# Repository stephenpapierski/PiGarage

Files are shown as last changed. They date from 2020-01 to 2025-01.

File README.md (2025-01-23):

> [!IMPORTANT]
> This never worked well and there are much better solutions out there. I would recommend taking a look at [Konnected](https://konnected.io/collections/shop-now?filter.p.tag=Smart+Garage+Door+Openers) Garage Door Openers, which support Hubitat, Home Assistant, Control4 and other cloud based home automation platforms.
# PiGarage
This project contains the Raspberry Pi and Hubitat driver code for a Raspberry Pi hat for controlling a garage door through Hubitat. The hardware includes a relay for actuating the garage door controller, 2 door sensor inputs (open/closed), and status LEDs to communicate door status.

See the [project wiki](https://github.com/stephenpapierski/PiGarage/wiki) to get started.

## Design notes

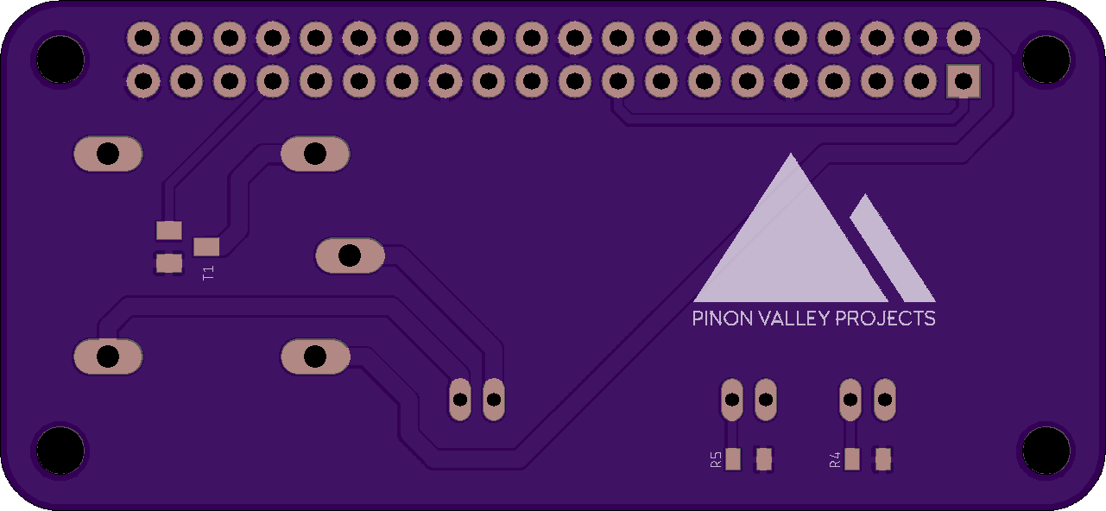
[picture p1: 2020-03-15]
pcb/PiGarage_RENDER_BOTTOM.png

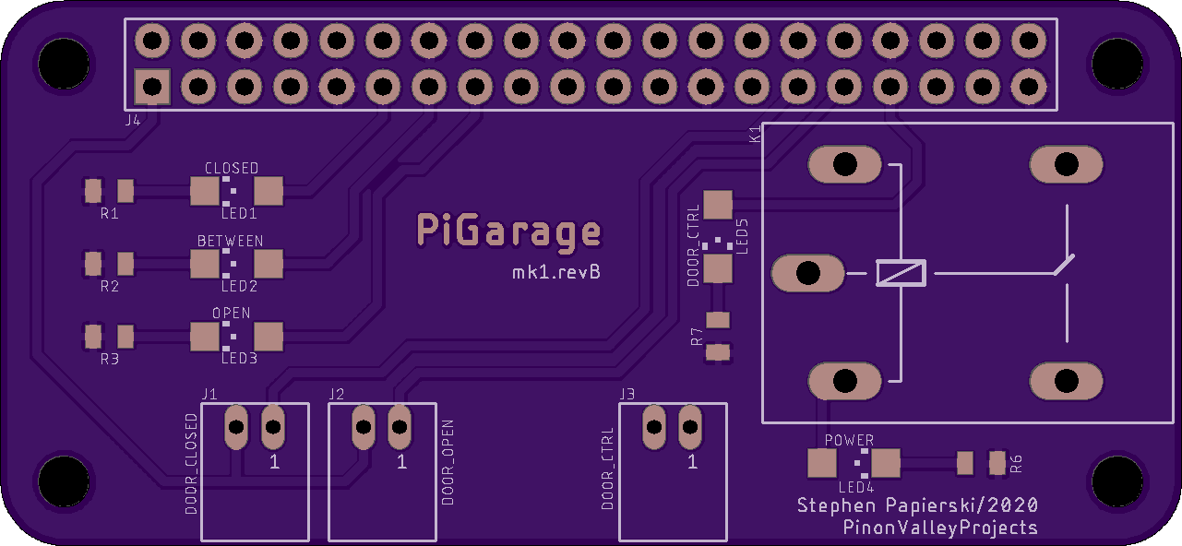
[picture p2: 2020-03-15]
pcb/PiGarage_RENDER_TOP.png

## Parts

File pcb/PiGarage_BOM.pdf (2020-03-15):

Description | Manufacturer | Part # | Device | Package Value Reference Designator Vendor Unit Cost Quantity Extended Cost Shipping Total | Link
2x20 Header | Pololu | 1037 RPI-GPIO-20x2 | J4 | Pololu | $1.25 | 1 | $1.25 | $1.25 https://www.pololu.com/product/1037
M2.5 Standoffs (4-pack) | Pololu | 1952 | | | | | Pololu | $1.39 | 1 | $1.39 | $1.39 https://www.pololu.com/product/1952
M2.5 Screws (25-pack) | Pololu | 1968 | | | | | Pololu | $0.99 | 1 | $0.99 | $0.99 https://www.pololu.com/product/1968
M2.5 Nuts (25-pack) | Pololu | 1967 | | | | | Pololu | $0.99 | 1 | $0.99 | $0.99 https://www.pololu.com/product/1967
$4.95 | $9.57
Relay | Omron | G5LE-1A4 DC5 | G5LE | | | K1 | Digi-Key | $1.41 | 1 | $1.41 | $1.41 https://www.digikey.com/product-detail/en/omron-electronics-inc-emc-div/G5LE-1A4-DC5/Z3116-ND/369019
Relay Driver | ON Semiconductor | NUD3105LT1G | NUD3105 | SOT23 | | T1 | Digi-Key | $0.44 | 1 | $0.44 | $0.44 https://www.digikey.com/product-detail/en/on-semiconductor/NUD3105LT1G/NUD3105LT1GOSCT-ND/1139972
120 Ohm LED Resistor | Yageo | AC0805FR-07120RL RESISTOR_0805 | 0805 | 120 | R2 | Digi-Key | $0.10 | 1 | $0.10 | $0.10 https://www.digikey.com/product-detail/en/yageo/AC0805FR-07120RL/YAG5353CT-ND/7063696
150 Ohm LED Resistor | Yageo | AC0805FR-07150RL RESISTOR_0805 | 0805 | 150 | R3 | Digi-Key | $0.10 | 1 | $0.10 | $0.10 https://www.digikey.com/product-detail/en/yageo/AC0805FR-07150RL/YAG3694CT-ND/6006543
200 Ohm LED Resistor | Yageo | AC0805FR-07200RL RESISTOR_0805 | 0805 | 200 | R1 | Digi-Key | $0.10 | 1 | $0.10 | $0.10 https://www.digikey.com/product-detail/en/yageo/AC0805FR-07200RL/YAG3707CT-ND/6006556
680 Ohm LED Resistor | Yageo | AC0805JR-07680RL RESISTOR_0805 | 0805 | 680 | R6 | Digi-Key | $0.10 | 1 | $0.10 | $0.10 https://www.digikey.com/product-detail/en/yageo/AC0805JR-07680RL/YAG3800CT-ND/6006649
10k Resistor | Yageo | AC0805FR-0710KL | RESISTOR_0805 | 0805 | 10k | R4, R5 | Digi-Key | $0.10 | 1 | $0.10 | $0.10 https://www.digikey.com/product-detail/en/yageo/AC0805FR-0710KL/311-10KLGCT-ND/2828155
Door Ctrl LED Resistor | DNP R7 | $0.00
Green Closed LED | Broadcom Limited | HSMG-C150 | CHIPLED_1206 | 1206 | | LED1 | Digi-Key | $0.50 | 1 | $0.50 | $0.50 https://www.digikey.com/product-detail/en/broadcom-limited/HSMG-C150/516-1443-1-ND/637767
Yellow In Between LED | Broadcom Limited | HSMY-C150 | CHIPLED_1206 | 1206 | | LED2 | Digi-Key | $0.53 | 1 | $0.53 | $0.53 https://www.digikey.com/product-detail/en/broadcom-limited/HSMY-C150/516-1442-1-ND/637766
Red Open LED | Broadcom Limited | HSMS-C150 | CHIPLED_1206 | 1206 | | LED3 | Digi-Key | $0.53 | 1 | $0.53 | $0.53 https://www.digikey.com/product-detail/en/broadcom-limited/HSMS-C150/516-1440-1-ND/637764
Blue PWR LED | Broadcom Limited | HSMN-C150 | CHIPLED_1206 | 1206 | | LED4 | Digi-Key | $1.05 | 1 | $1.05 | $1.05 https://www.digikey.com/product-detail/en/broadcom-limited/HSMN-C150/516-1446-1-ND/637770
Door Ctrl LED | DNP LED5 | $0.00
Door Sensor | SparkFun Electronics COM-13247 | Digi-Key | $3.50 | 2 | $7.00 | $7.00 https://www.digikey.com/product-detail/en/sparkfun-electronics/COM-13247/1568-1607-ND/7229877
JST Connector and Wire Assembly SparkFun Electronics PRT-09914 | JST_2PIN_HEADER | J1, J2, J3 | Digi-Key | $0.95 | 3 | $2.85 | $2.85 https://www.digikey.com/product-detail/en/sparkfun-electronics/PRT-09914/1568-1568-ND/6833927
| | | | | | | | | | | $8.99 $23.80
Circuit Board | Osh Park | PiGarage mk1.revA | $16.35 | 1 | $15.10 | $15.10 https://oshpark.com/shared_projects/nDRBJeuH
| | | | | | $0.00 $15.10
Total | $48.47

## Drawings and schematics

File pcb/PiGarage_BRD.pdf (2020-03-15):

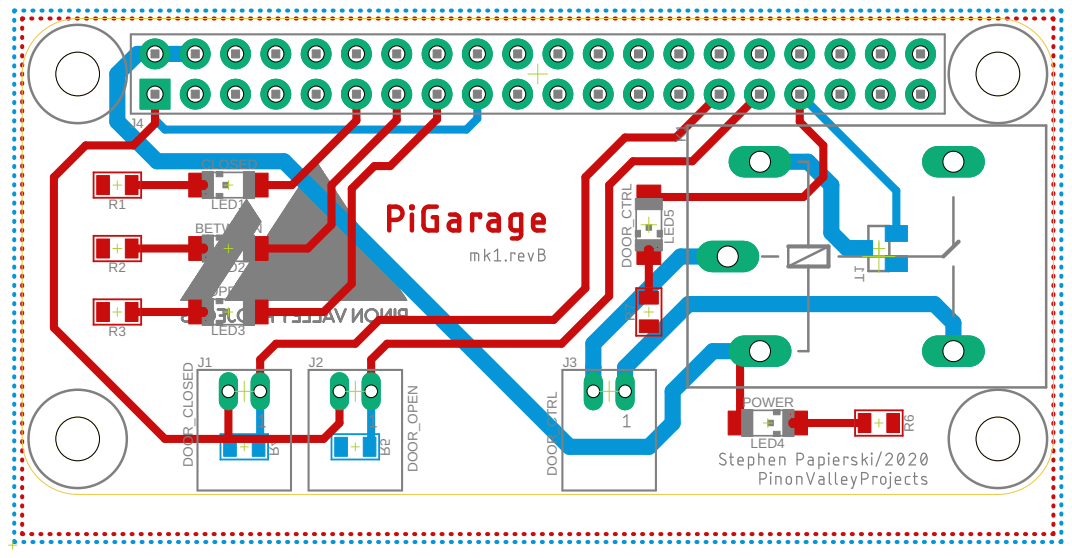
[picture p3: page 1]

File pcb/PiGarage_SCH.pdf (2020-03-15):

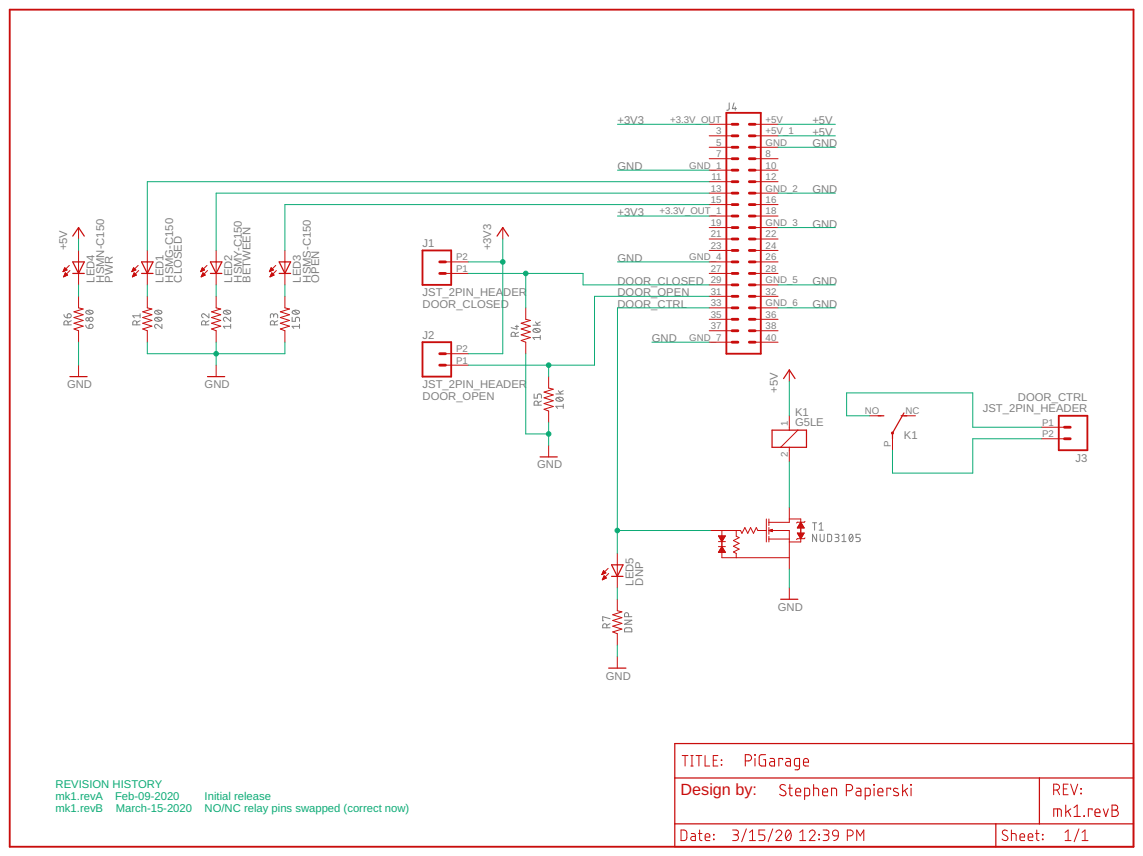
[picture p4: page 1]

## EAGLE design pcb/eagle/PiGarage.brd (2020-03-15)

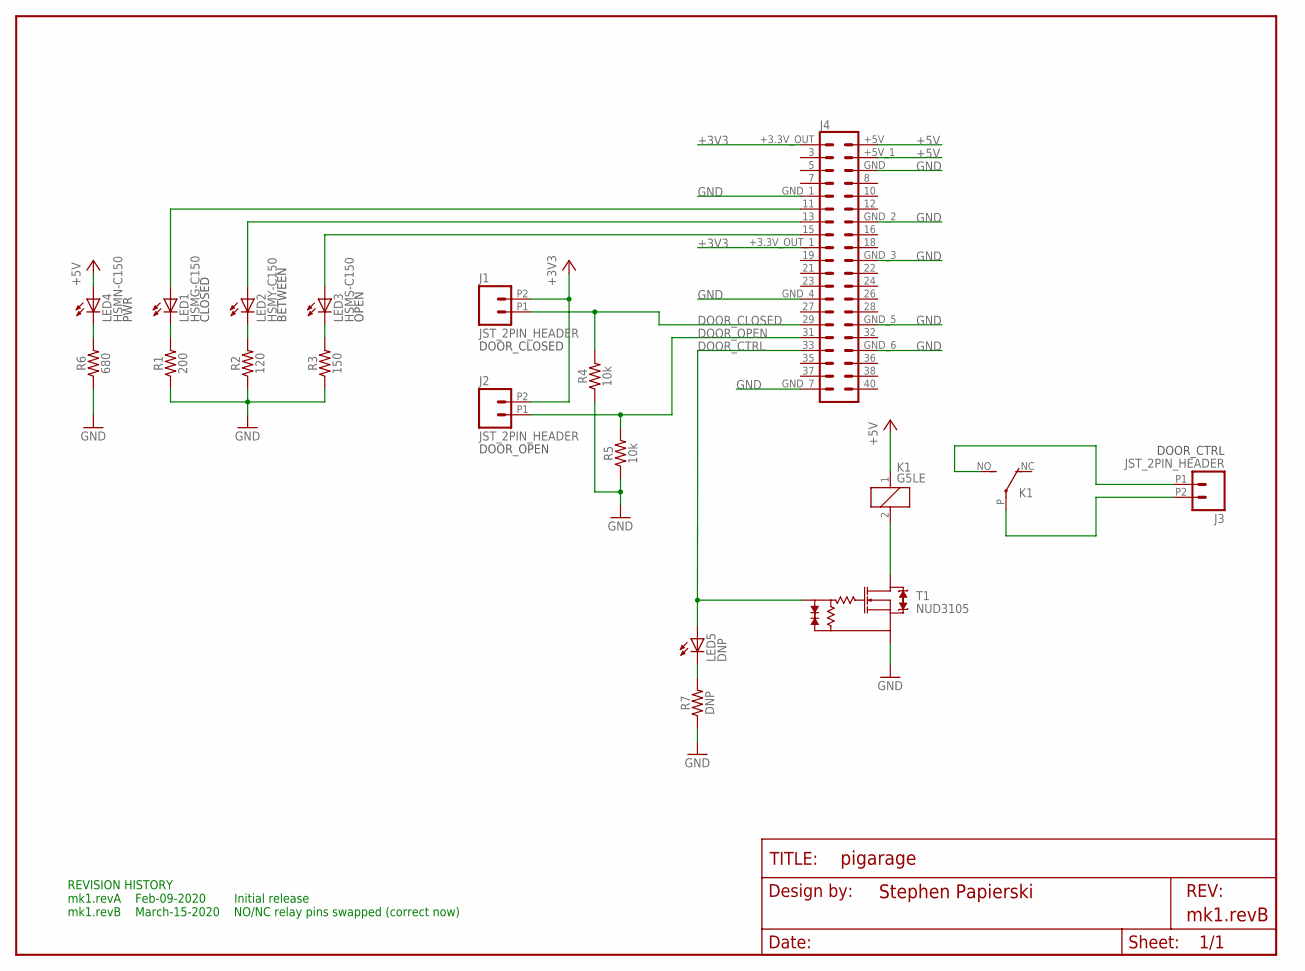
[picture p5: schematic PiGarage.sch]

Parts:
FRAME1: FRAME-LETTERNO_PACKAGE; DUMMY
J1, J2, J3: JST_2PIN_HEADER; JST_2PIN_RIGHT_HEADER
J4: RPI-GPIO-20X2
K1: G5LE
LED1: HSMG-C150; CHIPLED_1206
LED2: HSMY-C150; CHIPLED_1206
LED3: HSMS-C150; CHIPLED_1206
LED4: HSMN-C150; CHIPLED_1206
LED5: DNP; CHIPLED_1206
R1: 200; 0805
R2: 120; 0805
R3: 150; 0805
R4, R5: 10k; 0805
R6: 680; 0805
R7: DNP; 0805
T1: NUD3105; SOT23

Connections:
+3V3: J1.P2 (2), J2.P2 (2), J4.+3.3V_OUT (1), J4.+3.3V_OUT_1 (17)
+5V: J4.+5V (2), J4.+5V_1 (4), K1.1, LED4.A
DOOR_CLOSED: J1.P1 (1), J4.29, R4.2
DOOR_CTRL: J4.33, LED5.A, T1.1 (G)
DOOR_OPEN: J2.P1 (1), J4.31, R5.2
GND: J4.GND (6), J4.GND_1 (9), J4.GND_2 (14), J4.GND_3 (20), J4.GND_4 (25), J4.GND_5 (30), J4.GND_6 (34), J4.GND_7 (39), R1.1, R2.1, R3.1, R4.1, R5.1, R6.1, R7.1, T1.2 (S)
unnamed: K1.2, T1.3 (D)
unnamed: LED5.C, R7.2
unnamed: J3.P1 (1), K1.NO
unnamed: J3.P2 (2), K1.P
unnamed: LED4.C, R6.2
unnamed: J4.11, LED1.A
unnamed: J4.13, LED2.A
unnamed: J4.15, LED3.A
unnamed: LED1.C, R1.2
unnamed: LED2.C, R2.2
unnamed: LED3.C, R3.2

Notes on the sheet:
CLOSED
BETWEEN
OPEN
PWR
DOOR_CLOSED
DOOR_OPEN
DOOR_CTRL
REVISION HISTORY mk1.revA Feb-09-2020 Initial release mk1.revB March-15-2020 NO/NC relay pins swapped (correct now)

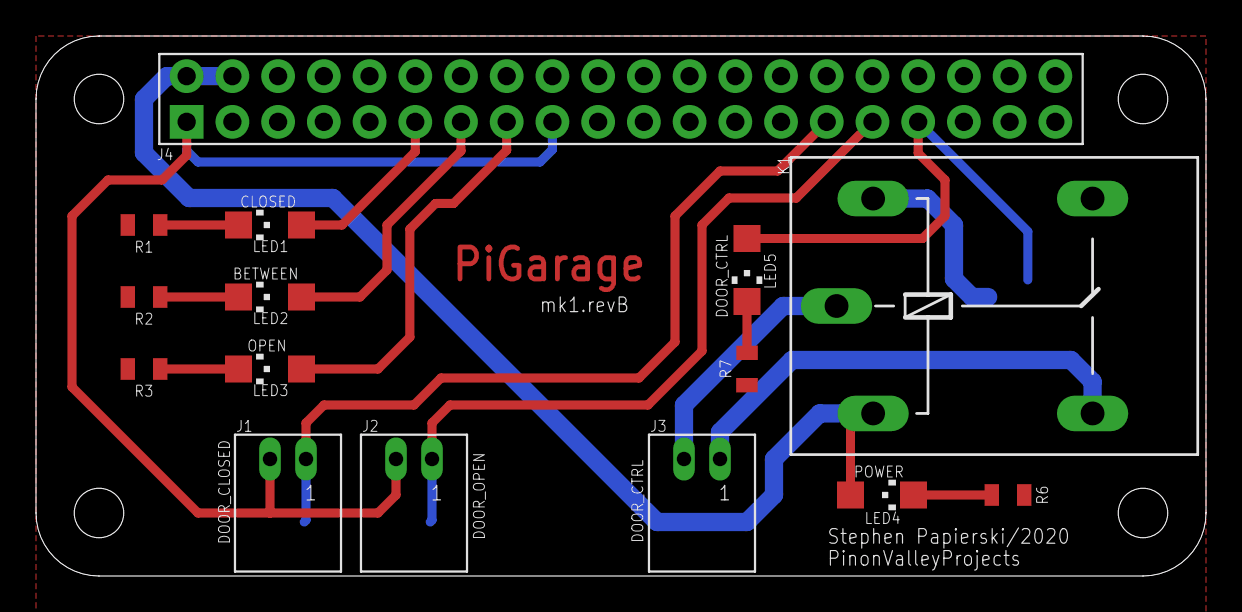
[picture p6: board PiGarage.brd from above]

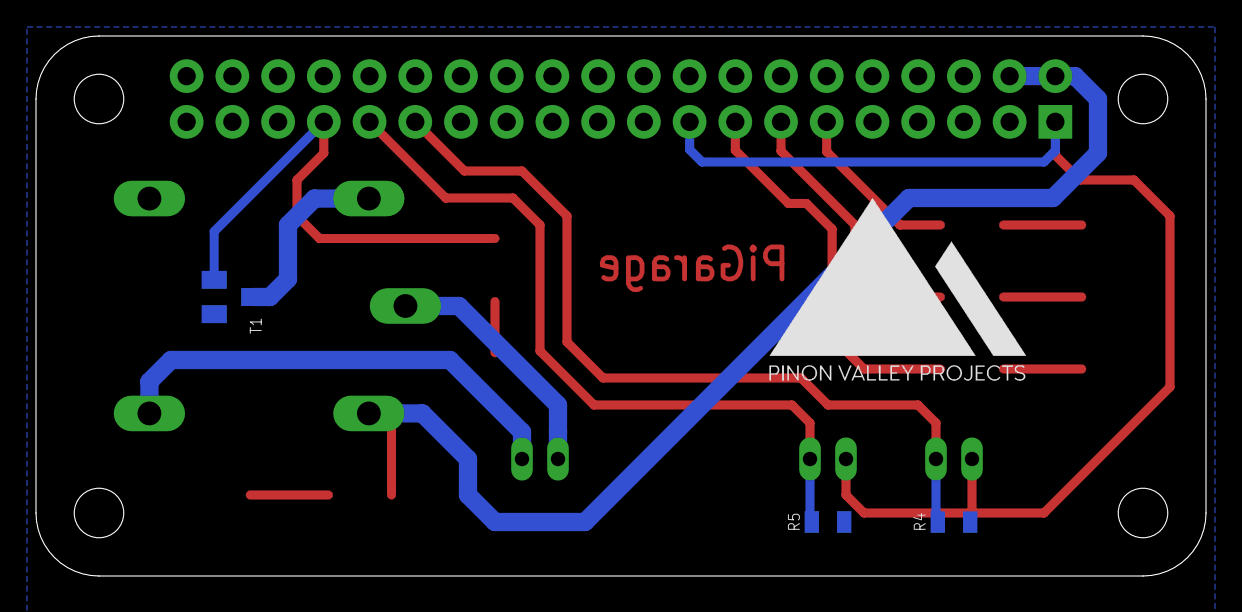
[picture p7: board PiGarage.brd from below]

Board: 2 copper layers, 65.0 x 30.0 mm, 19 parts (3 on the bottom side), 17 nets.

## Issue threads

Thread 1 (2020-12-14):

Service fails to restart on power failure

stephenpapierski, 2020-12-14:
Service tries to restart when device power is restored, but failed to do so. A service status reported `Start request repeated too quickly`.

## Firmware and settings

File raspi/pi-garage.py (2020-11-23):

#!/usr/bin/env python3
#
# PiGarage Smart Garage Door Controller
#
# Copyright 2020 Stephen Papierski
#
# Licensed under the GNU General Public License v3.0 (the "License"); you may not use this file except
# in compliance with the License. You may obtain a copy of the License at:
#
#     http://gnu.org/licenses/gpl-3.0.en.html
#
# Unless required by applicable law or agreed to in writing, software distributed under the License is distributed
# on an "AS IS" BASIS, WITHOUT WARRANTIES OR CONDITIONS OF ANY KIND, either express or implied. See the License
# for the specific language governing permissions and limitations under the License.
#
# Change History:
#
#   Date        Who                   What
#   ----        ---                   ----
#   2020-01-19  Stephen Papierski     Initial release
#   2020-11-22  Stephen Papierski     Making simpler and more reliable with single thread and interrupts
#  

import RPi.GPIO as GPIO
import requests
import time
import json
import threading
from flask import Flask, request
from os import path

class garageDoor():
    def __init__(self,closePin=29,openPin=31,relayPin=33,greenPin=11,yellowPin=13,redPin=15):
        #Setup pins and interrupt call backs
        GPIO.setup(closePin, GPIO.IN)
        GPIO.add_event_detect(closePin, GPIO.BOTH, callback=self._checkDoorChanged)
        GPIO.setup(openPin, GPIO.IN)
        GPIO.add_event_detect(openPin, GPIO.BOTH, callback=self._checkDoorChanged)
        GPIO.setup(relayPin, GPIO.OUT)
        GPIO.setup(greenPin, GPIO.OUT)
        GPIO.setup(yellowPin, GPIO.OUT)
        GPIO.setup(redPin, GPIO.OUT)

        self._closePin = closePin
        self._openPin = openPin
        self._relayPin = relayPin
        self._greenPin = greenPin
        self._yellowPin = yellowPin
        self._redPin = redPin
        self._status = None
        self._settingsFile = "piGarageSettings"
        self._hubIp = None
        # Run Configure with default params
        # If settings fail to load from file, set defaults
        if (self._readSettings()):
            print("No existing settings, writing default")
            self.setControls(transitionTime=15, actuateDuration=1000)

        self._checkDoorChanged(None)


    ##########################################################################
    # Public functions
    ##########################################################################

    """
    Update the configurable parameters of the sysem
    """
    def setControls(self, transitionTime=None, actuateDuration=None, hubIp=None):
        if (transitionTime):
            self._transitionTime = transitionTime
        if (actuateDuration):
            self._actuateDuration = actuateDuration
        if (hubIp):
            self._hubIp = hubIp

        self._writeSettings()

    """
    Get IP of the hubitat hub
    """
    def hubIp(self):
        return self._hubIp

    """
    Try to close the garage door
    """
    def closeDoor(self):
        print('Requesting door close')

        # if open -> actuate 1x
        if (self._status == "open"):
            self._actuateRelay()
            print ("Door closing")
        # if closed -> do nothing
        elif (self._status == "closed"):
            print ("Door already closed")
        # if opening -> actuate 2x
        elif (self._status == "opening"):
            self._doubleActuateDoor()
            print ("Door stopping then closing")
        # if closing -> do nothing
        elif (self._status == "closing"):
            print ("Door already closing")
        # if stopped -> actuate 1x
        elif (self._status == "stopped"):
            self._actuateRelay()
            print("Door closing")
        else:
            print("Door in unknown state, actuating relay")
            self._actuateRelay()

    """
    Try to open the garage door
    """
    def openDoor(self):
        print('Requesting door open')

        # if open -> do nothing
        if (self._status == "open"):
            print ("Door already open")
        # if closed -> actuate 1x
        elif (self._status == "closed"):
            self._actuateRelay()
            print ("Door opening")
        # if opening -> do nothing
        elif (self._status == "opening"):
            print ("Door already opening")
        # if closing -> actuate 1x
        elif (self._status == "closing"):
            self._actuateRelay()
            print ("Door opening")
        # if stopped -> actuate 2x
        elif (self._status == "stopped"):
            self._doubleActuateDoor()
            print ("Door closing then opening")
        else:
            print ("Door in unknown state, actuating relay")
            self._actuateRelay()

    def refreshHubitat(self):
        if (self._hubIp):
            url = 'http://'+self._hubIp+':39501'
            body = {'status':self._status,'isNew':False}
            r = requests.post(url, json=body)
            print("Sending refresh status (" + self._status +") to hub (" + str(self._hubIp) + ")")


    ##########################################################################
    # Internal functions
    ##########################################################################

    """
    Actuate the relay to open/close door
    """
    def _actuateRelay(self):
        print("Actuating Relay...")
        GPIO.output(self._relayPin, GPIO.HIGH)
        time.sleep(float(self._actuateDuration)/1000)
        GPIO.output(self._relayPin, GPIO.LOW)

    """
    Double actuate the relay to open/close door
    """
    def _doubleActuateDoor(self):
        self._actuateRelay()
        time.sleep(self._actuateDuration/1000)
        self._actuateRelay()

    """
    Write hubitat settings to the settings file
    """
    def _writeSettings(self):
        print("Writing settings...")
        settings = {}
        settings['transitionTime'] = self._transitionTime
        settings['actuateDuration'] = self._actuateDuration
        settings['hubIp'] = self._hubIp
        with open(self._settingsFile, "w") as outfile:
            json.dump(settings, outfile)

        print("transitionTime = " + str(self._transitionTime) + "s")
        print("actuateDuration = " + str(self._actuateDuration) + "ms")
        print("hubIp = " + str(self._hubIp))

    """
    Read hubitat settings from the settings file
    """
    def _readSettings(self):
        if (path.exists("./" + self._settingsFile)):
            print("Reading in settings...")
            with open(self._settingsFile, "r") as json_file:
                data = json.load(json_file)
                self._transitionTime = data['transitionTime']
                self._actuateDuration = data['actuateDuration']
                self._hubIp = data['hubIp']

            print("transitionTime = " + str(self._transitionTime) + "s")
            print("actuateDuration = " + str(self._actuateDuration) + "ms")
            print("hubIp = " + str(self._hubIp))
            return 0
        else:
            return 1

    """
    Update the LED indicators based on the status
    """
    def _updateStatusLeds(self, status):
        # Reset all status leds
        leds = (self._greenPin, self._yellowPin, self._redPin)
        GPIO.output(leds, GPIO.LOW)

        # if open -> red led
        if (status == "open"):
            setLeds = (self._redPin)
        # if closed -> green led
        elif (status == "closed"):
            setLeds = (self._greenPin)
        # if opening or closing -> yellow led
        elif (status == "opening" or self._status == "closing"):
            setLeds = (self._yellowPin)
        # if stopped -> yellow and red
        elif (status == "stopped"):
            setLeds = (self._yellowPin, self._redPin)
        elif (status == "unknown"):
            setLeds = (self._greenPin, self._yellowPin, self._redPin)
        else:
            setLeds = None
            print ("Unknown LED state")

        if (setLeds):
            GPIO.output(setLeds, GPIO.HIGH)

    """
    Handler for when the door opens or closes. This should be called at startup and when
    the interrupt handler for the door stat sensors fire.
    """
    def _checkDoorChanged(self, pin):
        doorClosed = GPIO.input(self._closePin)
        doorOpen = GPIO.input(self._openPin)
        newStatus = None

        # Door is closed
        if (doorClosed and not doorOpen):
            if (self._status != "closed"):
                newStatus = "closed"
                print("Status: Door is closed")
        # Door is open
        elif (doorOpen and not doorClosed):
            if (self._status != "open"):
                newStatus = "open"
                print("Status: Door is open")
        # Somewhere in between
        elif (not doorOpen and not doorClosed):
            if (pin == self._closePin and self._status == "closed"):
                newStatus = "opening"
                print("Status: Door is opening")
                # Check if door stopped after transitionTime
                threading.Timer(self._transitionTime, self._doorStopped).start()
            elif (pin == self._openPin and self._status == "open"):
                newStatus = "closing"
                print("Status: Door is closing")
                # Check if door stopped after transitionTime
                threading.Timer(self._transitionTime, self._doorStopped).start()
            elif (pin == None):
                # this only happens during startup when pin = None (not an interrupt)
                newStatus = "open"
                print("Status: Pin is None, Door is unknown, assume open")
        elif (doorOpen and doorClosed):
            self._status = "unknown"
            print("Status: Door is unknown")
        else:
            self._status = "unknown"
            print("This shouldn't happen, setting door to unknown")


        if (newStatus):
            self._updateStatusAll(newStatus)

    """
    This should be called after a timer interupt. If the door hasn't finish opening or
    closing, it will assume the door has stopped open, and report open.
    """
    def _doorStopped(self):
        if (self._status != "open" and self._status != "closed"):
            print("Door stopped, reporting open")
            self._updateStatusAll("open")

    """
    Update the local status, Hubitat status, and LED status
    """
    def _updateStatusAll(self, newStatus):
        self._status = newStatus
        self._updateStatusLeds(newStatus)
        if (self._hubIp):
            url = 'http://'+self._hubIp+':39501'
            body = {'status':newStatus,'isNew':True}
            r = requests.post(url, json=body)
            print("Sending status (" + newStatus +") to hub (" + str(self._hubIp) + ")")

# Main Program
# Flask app for receiving POST Requests
app = Flask(__name__)
@app.route('/PiGarage/open/', methods=['POST'])
def open_command():
    garage.openDoor()
    # Update hub ip
    if (not garage.hubIp()):
        garage.setControls(hubIp=request.remote_addr)
    return {'status':'Opening Garage Door...'}

@app.route('/PiGarage/close/', methods=['POST'])
def close_command():
    garage.closeDoor()
    # Update hub ip
    if (not garage.hubIp()):
        garage.setControls(hubIp=request.remote_addr)
    return {'status':'Closing Garage Door...'}

@app.route('/PiGarage/configure/', methods=['POST'])
def configure_command():
    data = request.get_json()
    transitionTime = data['transitionTime']
    actuateDuration = data['actuateDuration']
    hubAddr = request.remote_addr
    garage.setControls(transitionTime=transitionTime, actuateDuration=actuateDuration, hubIp=hubAddr)
    return {'status':'Configuring...'}

@app.route('/PiGarage/refresh/', methods=['POST'])
def refresh():
    # Update hub ip
    if (not garage.hubIp()):
        garage.setControls(hubIp=request.remote_addr)
    garage.refreshHubitat()
    return {'status':'Refreshing Hubitat...'}

if __name__ == '__main__':
    GPIO.setmode(GPIO.BOARD)
    garage = garageDoor(closePin =  29, 
                        openPin  =  31, 
                        relayPin =  33)
    app.run(host='0.0.0.0')

print("Cleaning up GPIO")
GPIO.cleanup()

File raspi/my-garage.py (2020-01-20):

#!/usr/bin/env python3
import gpiozero
from flask import Flask, request

class distanceSensor(gpiozero.MCP3001):
    def __init__(self, max_voltage=3.3, **spi_args):
        super(distanceSensor, self).__init__(max_voltage, **spi_args)

    @property
    def distanceCM(self):
        return self.raw_value
    @property
    def closed(self):
        return self.value >= 1000
    @property
    def open(self):
        return self.value <= 100

# Main Program
app = Flask(__name__)
@app.route('/myGarage/open/', methods=['POST'])
def open():
    print(request.form)
    return 'Opening Garage Door...'

@app.route('/myGarage/close/', methods=['POST'])
def close():
    print(request.form)
    return 'Closing Garage Door...'

if __name__ == '__main__':
    app.run(host='0.0.0.0')
#distanceS = distanceSensor(max_voltage = 3.3,
#                             clock_pin = 11,
#                             mosi_pin = 10,
#                             miso_pin = 9,
#                             select_pin = 7)
#
#
#while (True):
    #pass
#    print("raw: \t" + str(distanceS.raw_value))
#    print("CM: \t" + str(distanceS.distanceCM))
#    print("Closed: \t" + str(distanceS.closed))
#    print("Open: \t" + str(distanceS.open))

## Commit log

2019-03-04 Start of distance sensor class
2020-01-20 Organizing files into hubitat drivers and raspi program
2020-01-20 Adding ability to handle POST requests from the raspberry pi side
2020-01-20 Adding hubitat driver code to set POST requests for open and close
2020-01-22 Driver parse method can now parse incoming http post json content
2020-01-24 Added garageDoor class to handle sensor interaction and logic
2020-01-24 Hubitat driver updates current state from raspi post requests
2020-02-01 Added stopped status, relay logic based on status, and a timeout value.
2020-02-02 Added status led logic
2020-02-09 Fixing issue where unknown state was continuously reported
    [pi-garage.py]
2020-02-10 Grabbing hub ip from post messages so the hub ip is no longer hard coded
    [pi-garage.py]
2020-02-11 Adding pcb files
    [PiGarage.brd, PiGarage.sch]
2020-02-13 Adding formatted BOM and board renders
    [PiGarage_BOM.xlsx]
2020-03-15 Fixed relay NC/NO pin swap issue, bumped board rev to mk1.revB
    [PiGarage.brd, PiGarage.sch, PiGarage_BOM.xlsx]
2020-03-15 Increasing resolution of board renders
2020-11-23 Making simpler and more reliable with single thread and interrupts

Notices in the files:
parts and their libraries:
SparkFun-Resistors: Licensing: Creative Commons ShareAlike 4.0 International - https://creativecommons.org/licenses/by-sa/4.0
